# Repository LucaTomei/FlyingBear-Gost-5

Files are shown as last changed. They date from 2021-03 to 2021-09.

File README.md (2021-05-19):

# FlyingBear-Gost-5

This repository contains structural and firmware side changes applicable on the Flyingbear Ghost 5 3D printer.
The changes on the software side can be applied on the STOCK version printer or with TMC2209 driver changes.

## [Ricambi e upgrades](https://www.1612.it/wp/ricambi-e-upgrades-flying-bear-ghost-5/)

## Repository Content

- **[Firmwares](Firmwares)**
- **[Projects](Projects)**
- **[Installation Videos](Installation_Videos)**
- **[Guides](Guides)**
- **[Slicers](Slicers/README.md)**
- **[Other](Other)**

## Useful Links

- [Calibrazione Step](https://www.stampa3d-forum.it/articoli/guide/regolazione-step-mm-guida-calibrazione-assi-x-y-z/)
- [**Italy Makers - Flying Bear Ghost Facebook group**](/groups/907067056500590)
- [**Flyingbear Italian Community**](https://fbghostita.miraheze.org/wiki/Pagina_principale)
- [Russian Wiki](https://flyingbear.info/ru/решения)
- **GCODE Analyzer**
    - [Online version](http://www.gcodeanalyser.com)
    - [GitHub Repo](https://github.com/syue87/GCodeAnalyser)

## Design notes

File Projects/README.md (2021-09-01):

# Projects for Flyingbear Ghost 5

## [Smart Led](Smart_Led/README.md)

## [Octoprint PSU control case](Octoprint_PSU/README.md)

## [Russian Upgrades](CHUCHATV_Upgrades)

## [Manual Bed Leveling Project](Bed_Leveling/README.md)

### Case

- [Case in this repository with gcode files](Copertura_plexiglass/README.md)
- [Case with door](https://www.thingiverse.com/thing:4190488)

### Tool Holders

- [Tool Stand 1](https://www.thingiverse.com/thing:4067472)
- [Tool Stand 2](https://www.thingiverse.com/thing:4045895)
- [Tool Stand 3](https://www.thingiverse.com/thing:3548716)
- [Tool Stand 4](https://www.thingiverse.com/thing:4265119)
- [Tool Stand 5 - For Thermalbox](https://www.thingiverse.com/thing:4794188)
- [Tool Stand 6](https://www.thingiverse.com/thing:4736121)

### CLips 
- [Clip for extruder](https://www.thingiverse.com/thing:4267787)
- [Filament Holder](https://www.thingiverse.com/thing:4749552)
- [Bowdend Clip](https://www.thingiverse.com/thing:4613639)

### Cameras
- [Raspberry Infrared Camera](Raspberry_Infrared_cam/README.md)
- [Raspberry Cam](Raspberry_Cam/README.md)
- 
- [My Esp32 camera holder]()
- [Camera Holder - Logitech C525](https://www.thingiverse.com/thing:4667948)
- [Camera Holder - Pi Camera](https://www.thingiverse.com/thing:4390399/files)
- [Esp Camera](https://www.thingiverse.com/thing:4713405)
- [IP Camera Holder](https://www.thingiverse.com/thing:4779987)

### Printer Parts

- [Printer Foot 1](https://www.thingiverse.com/thing:4683217)
- [Printer Foot 2](https://www.thingiverse.com/thing:4702313)
- [Micro SD Holder](https://www.thingiverse.com/thing:4707808)
- [Filament Guide](https://www.thingiverse.com/thing:4704848)
- [Z Axis Support](https://www.thingiverse.com/thing:4686040)
- [Adjustable Bed Screw](https://www.thingiverse.com/thing:4583235)
- [Touchpen Holder 1](https://www.thingiverse.com/thing:4691468)
- [Touchpen Holder 2](https://www.thingiverse.com/thing:4606683)
- [Screen Cover](https://www.thingiverse.com/thing:4238913)

## [Oversized Fan Mod](ventola_maggiorata/README.md)

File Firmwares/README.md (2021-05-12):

# Firmwares for Flyingbear Ghost 5

[Official Firmwares Link](https://drive.google.com/drive/u/0/folders/1ZUuk_V8Bdn0Vt0OC19J2wQ0Nd3v5MbL4)

## Original Drivers

 - [STOCK v 5.9.1](Original_Drivers/Ghost_5_firmwarev5.91.zip)
 - [STOCK v 5.8](Original_Drivers/Ghost_5_firmware_V5-8.zip)
 - [Original with 5-point calibration (v. 5.8)](Original_Drivers/Ghost_5_firmware_V5-8-Modificato.zip)
 - [Original with 5-point calibration (v. 5.9.1)](Original_Drivers/Ghost_5_firmware_V5-91-Modificato.zip)
 - [Simone Carnio Firmware](Original_Drivers/STOCK_Firmware_Simone_Carnio_GH5.zip)

## For TMC2209

- [Original with 5-point calibration (v. 5.9.1) with all TMC2209](TMC22XX/Ghost_5_firmware_V5-91[TMC2209]-Modificato.zip)
- [Red Edition](TMC22XX/Flying-Bear-Ghost-5-Marlin-2.0-Firmware-Red3D-Edition-1.0.3.zip)

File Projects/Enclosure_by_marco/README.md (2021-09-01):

# FlyingBear Ghost 5 enclosure: top cover and front cover/door

Finally I decided to buy another 3D printer, this time I choose the FlyingBear Gost 5. I buy it because for 250 € it has solved many problems of other printers like Ender or Artillery (with the same price).

I made a case because I would like to print a more dangerous material like ABS, and to do that I create two different rears of the top cover, one standard and one with a fan for extracting harmful fumes.

<ol><li><a rel="noreferrer noopener" href="https://www.mischianti.org/2021/07/05/flyingbear-ghost-5-enclosure-top-cover/" target="_blank">FlyingBear Ghost 5 enclosure: top cover</a></li><li><a href="https://www.mischianti.org/2021/07/09/flyingbear-ghost-5-enclosure-front-cover-door/" target="_blank" rel="noreferrer noopener">FlyingBear Ghost 5 enclosure: front cover/door</a></li></ol>

FlyingBear Ghost 5 enclosure photo

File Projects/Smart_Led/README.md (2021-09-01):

# Ikea Dioder - Versione Smart

Questo progetto è nato per poter alimentare direttamente, tramite il pin vuoto della stampante, delle semplici strisce LED (non smart) rendendole smart attraverso un relè.

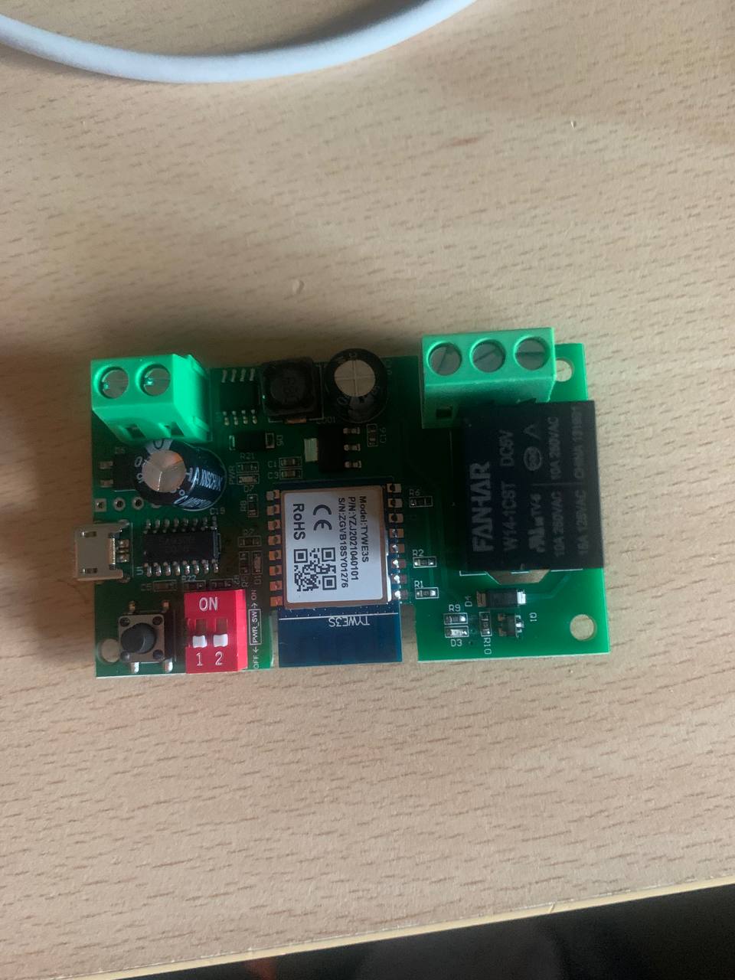
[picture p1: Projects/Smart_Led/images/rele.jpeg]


Consiglio: Dato che il relè in questione può anche essere alimentato via usb vi consiglio di configurarlo con la sua app nativa (SmartLife) prima di effettuare il cablaggio tramite stampante in modo tale che una volta effettuato il collegamento dei cavi elettrici il tutto sia già configurato e pronto all'uso.

## Occorrente

- [Ikea Dioder](https://www.ikea.com/us/en/p/dioder-led-4-piece-light-strip-set-white-20119418/) o qualsiasi altra striscia led 
- [Relé SmartLife](https://www.amazon.it/gp/product/B07SNBKXH5/ref=ppx_yo_dt_b_asin_title_o00_s00?ie=UTF8&psc=1) o qualsiasi altro relè smart
- Cavi connettore JST XH2.54 2 pin:
    - [Link Aliexpress](https://it.aliexpress.com/item/32954418743.html?spm=a2g0s.9042311.0.0.27424c4djxtsz4)
    - [Link Amazon](https://www.amazon.it/Connettore-Connettori-Espansione-Intestazione-XH2-54-2P/dp/B08P3JN1MQ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ÅMÅŽÕÑ&dchild=1&keywords=JST+XH2.54&qid=1630515821&sr=8-1)
- Comune nastro isolante

## Schema Cablaggio

Per cablare il tutto puoi scegliere se alimentare il relè e i led ad esso collegati connettendo il relè direttamente ad un pin della scheda madre oppure se alimentarlo tramite alimentatore della stampante. Di seguito verranno mostrate le due modalità di montaggio:

### Collegamento tramite alimentatore

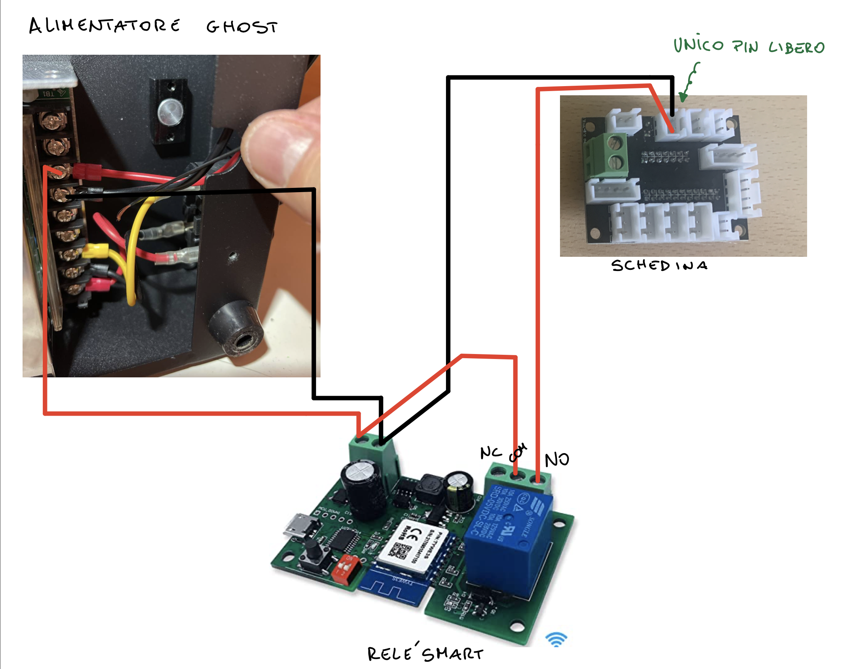
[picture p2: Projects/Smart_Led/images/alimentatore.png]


### Collegamento tramite pin della scheda madre

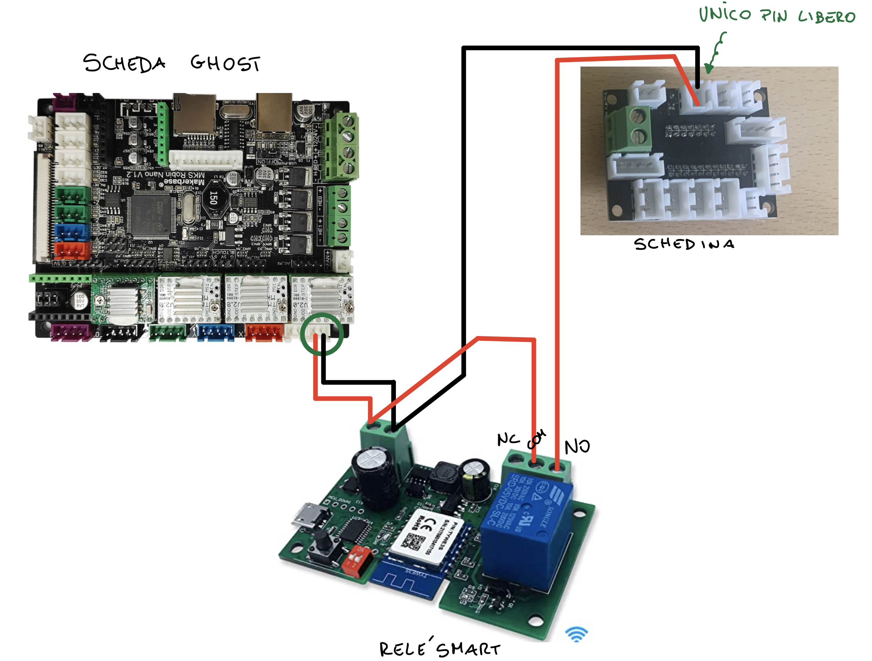
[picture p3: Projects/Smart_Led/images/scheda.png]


## Risultato Finale

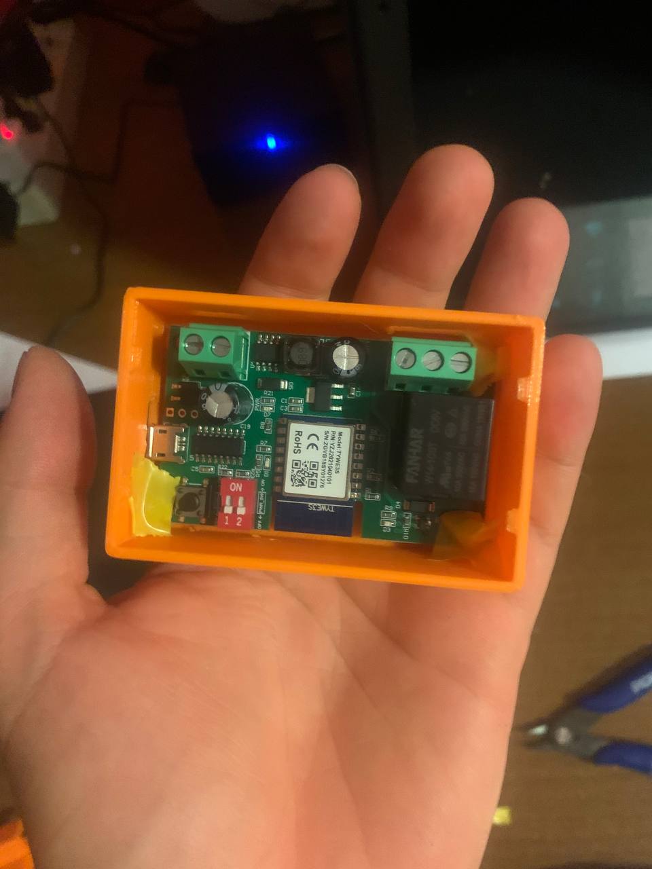
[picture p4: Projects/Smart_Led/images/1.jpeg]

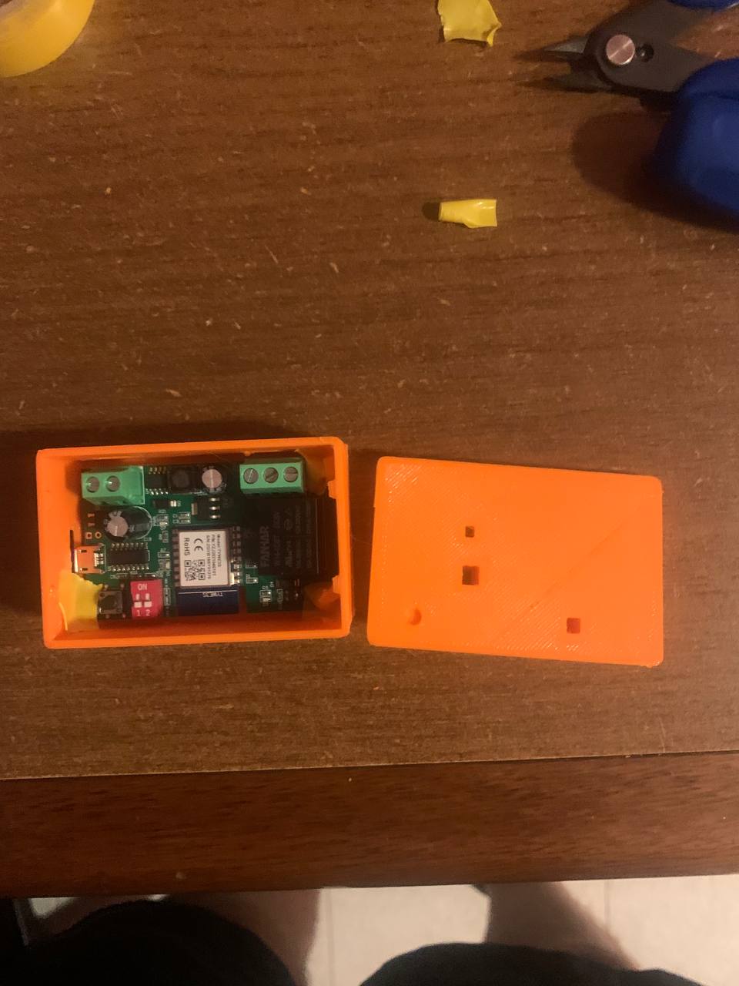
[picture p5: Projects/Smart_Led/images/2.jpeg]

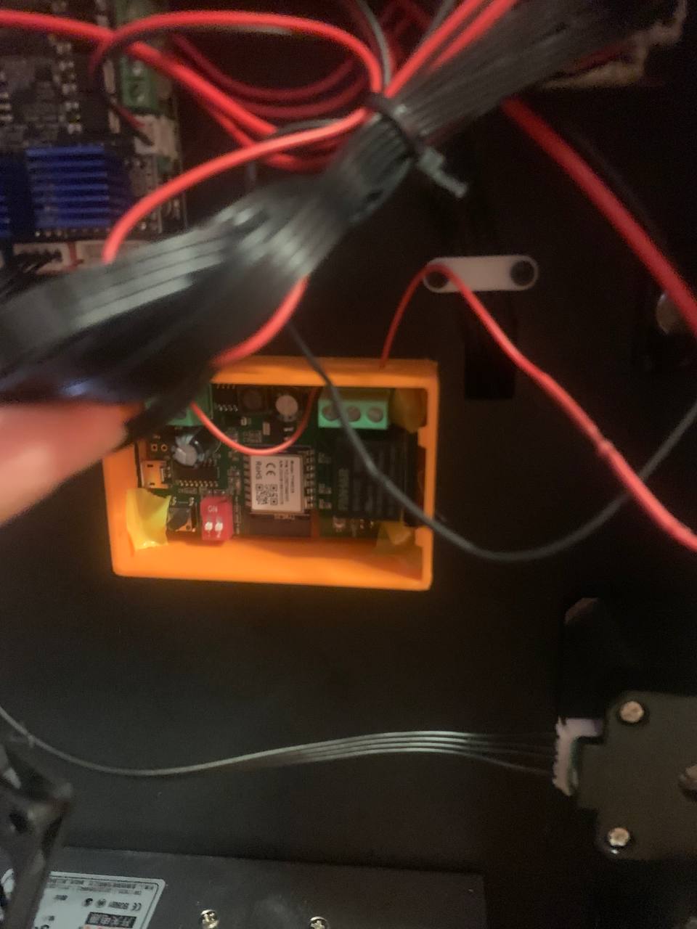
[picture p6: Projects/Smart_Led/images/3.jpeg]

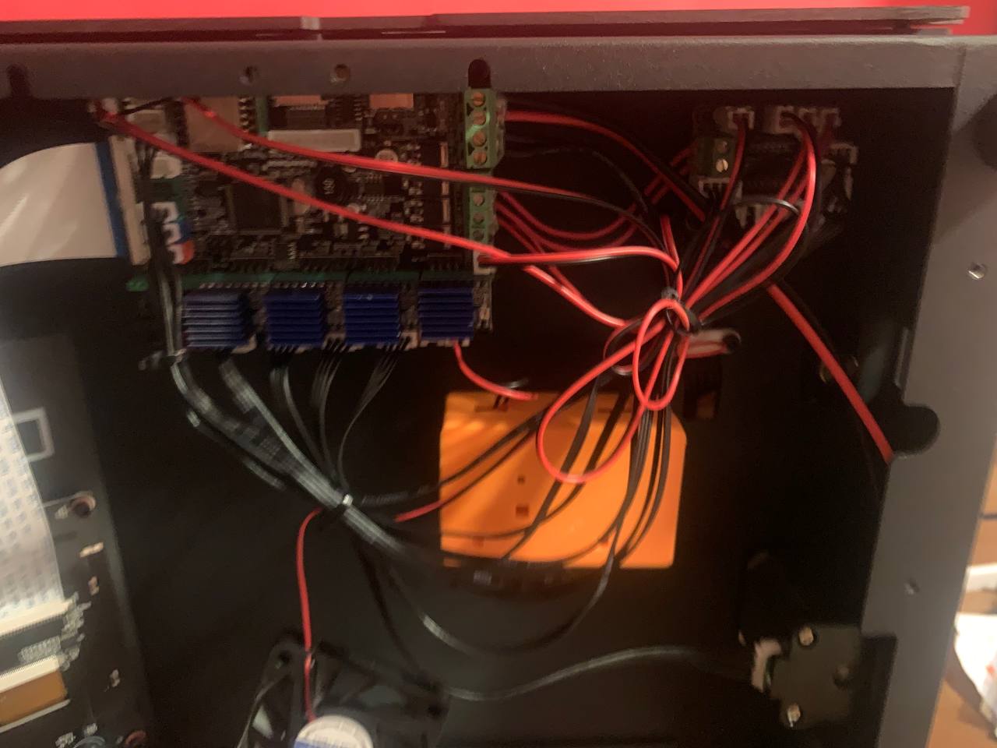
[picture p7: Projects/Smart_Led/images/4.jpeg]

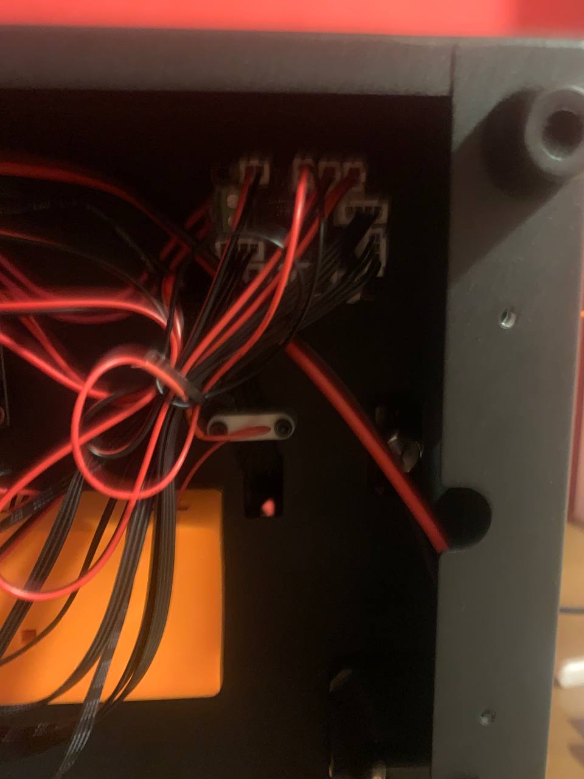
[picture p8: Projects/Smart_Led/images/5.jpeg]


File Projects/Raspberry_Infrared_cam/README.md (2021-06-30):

# Raspberry Infrared Camera Mount For Flyingbear Ghost 5

## Risultato Finale (Montaggio Alto)

<p align="center">
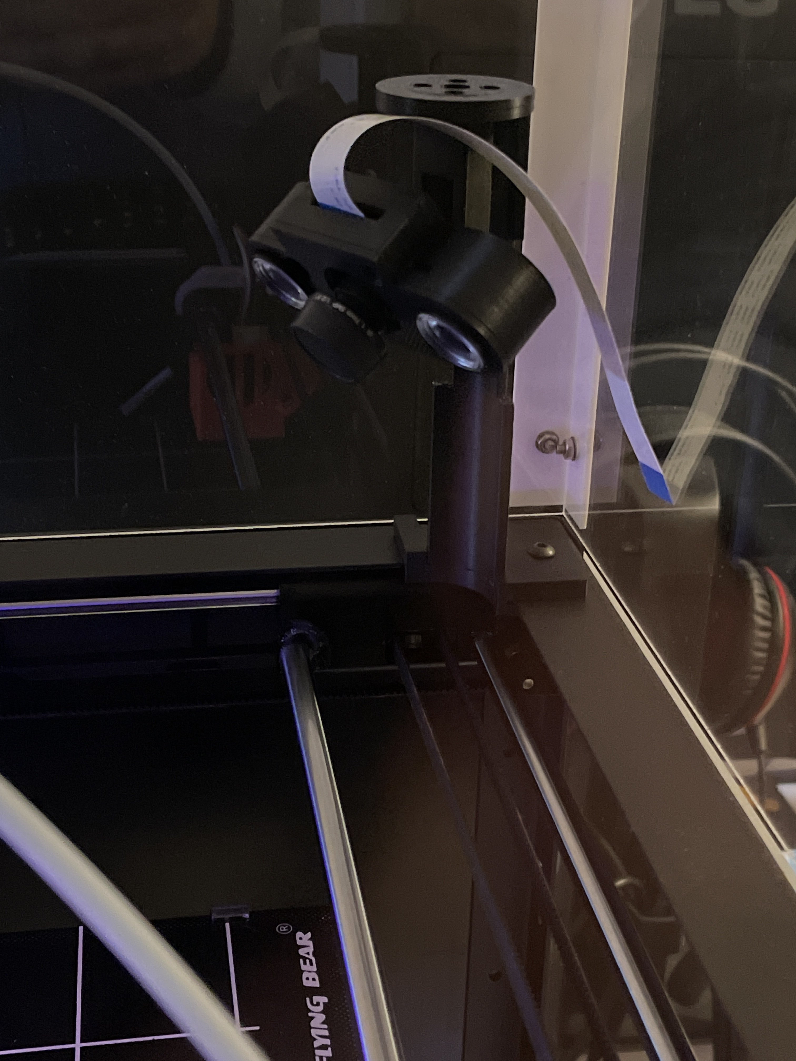
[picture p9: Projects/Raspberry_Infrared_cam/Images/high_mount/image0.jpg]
  
</p>

<p align="center">
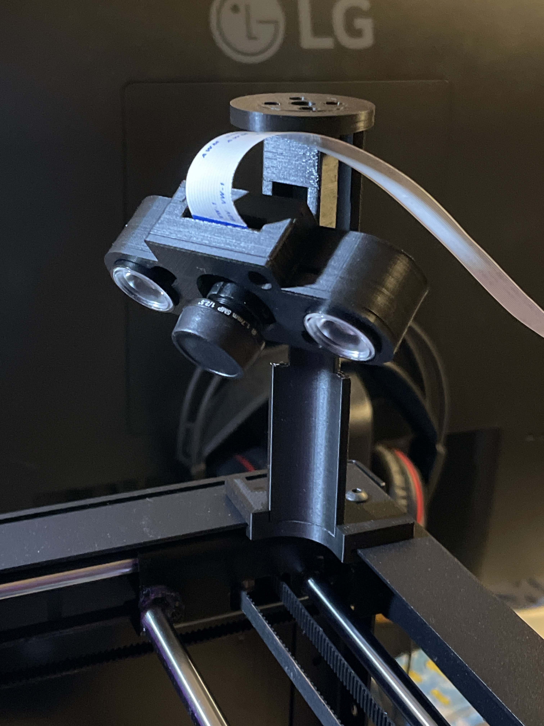
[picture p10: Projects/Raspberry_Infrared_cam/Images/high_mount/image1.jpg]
  
</p>

<p align="center">
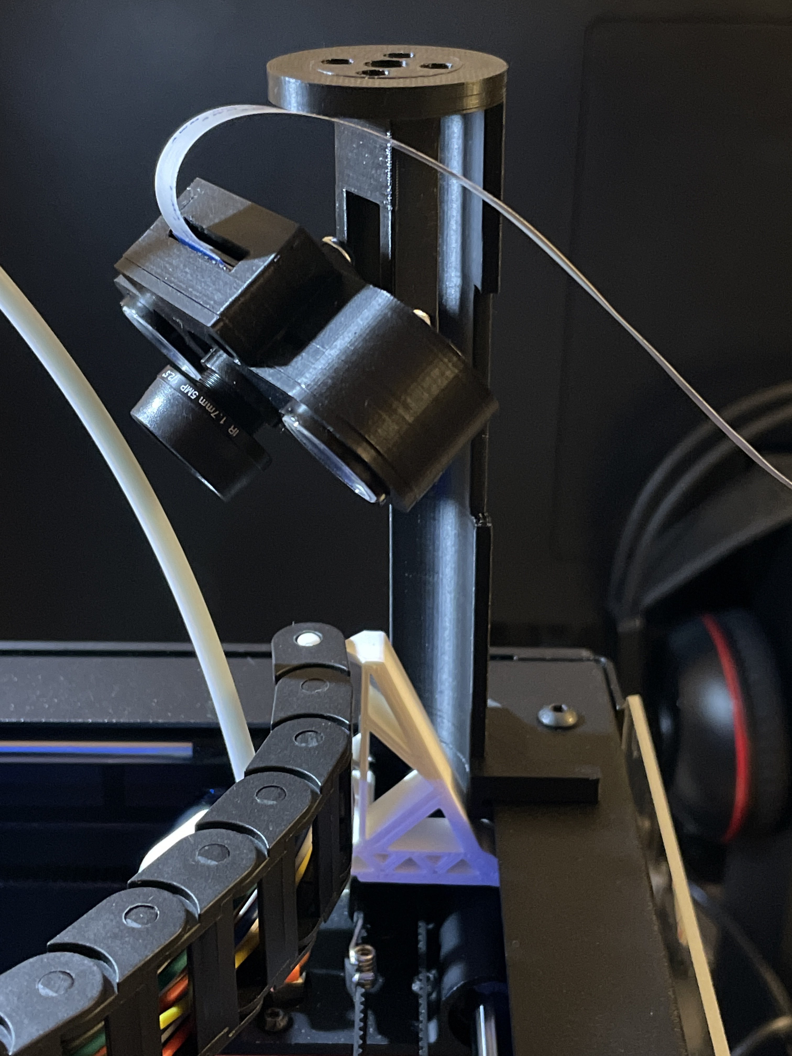
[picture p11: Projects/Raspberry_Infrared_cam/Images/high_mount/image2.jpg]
  
</p>

## Stl Files (Montaggio Alto)

- [Staffa Snodo.stl](stls/high_mount/Staffa_Snodo.stl)
- [Braccio Snodo.stl](stls/high_mount/braccio_snodo.stl)
- [Base Cover.stl](stls/high_mount/base_cover.stl)
- [Coperchio](stls/high_mount/coperchio.stl)
- [Base Supporto Angolo](stls/high_mount/base_supporto_angolo.stl)
- [Staffa Supporto Angolo](stls/high_mount/staffa_supporto_angolo.stl)

## Risultato Finale (Montaggio Piatto)

<p align="center">
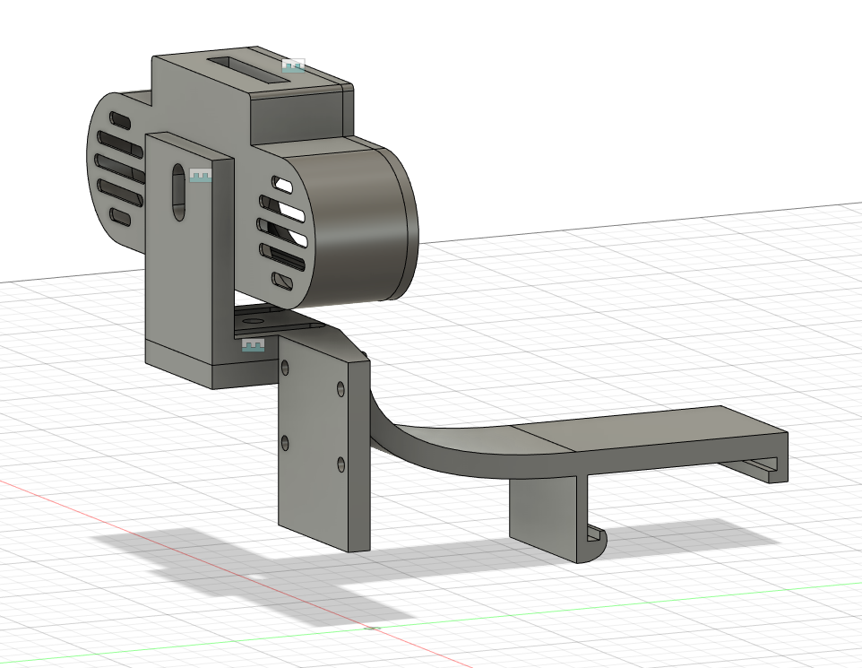
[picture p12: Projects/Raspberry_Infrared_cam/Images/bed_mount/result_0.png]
  
</p>

<p align="center">
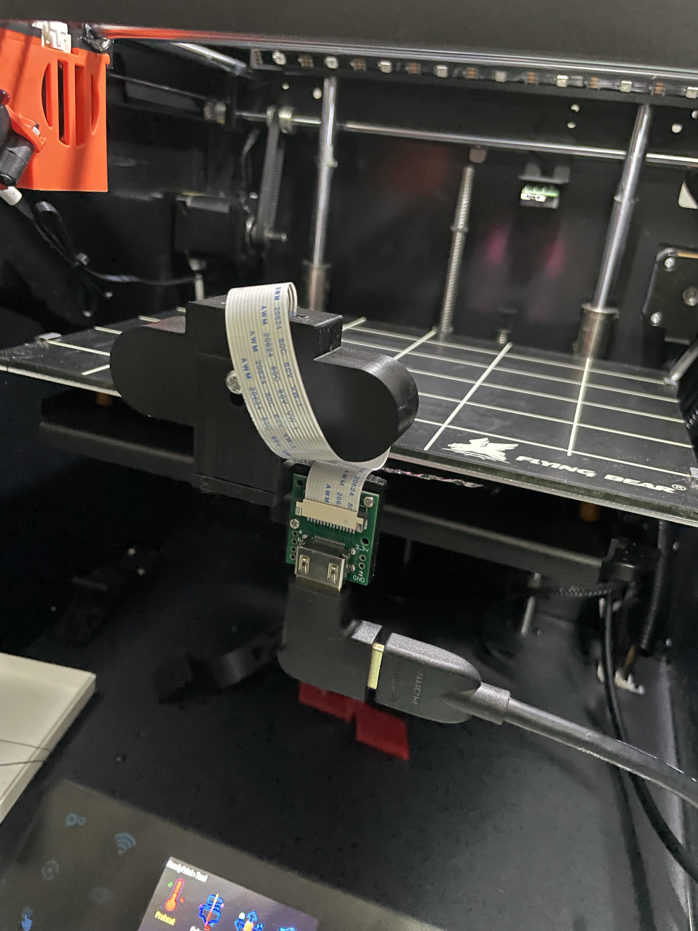
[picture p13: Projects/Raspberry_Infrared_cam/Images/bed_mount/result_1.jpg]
  </p>

<p align="center">
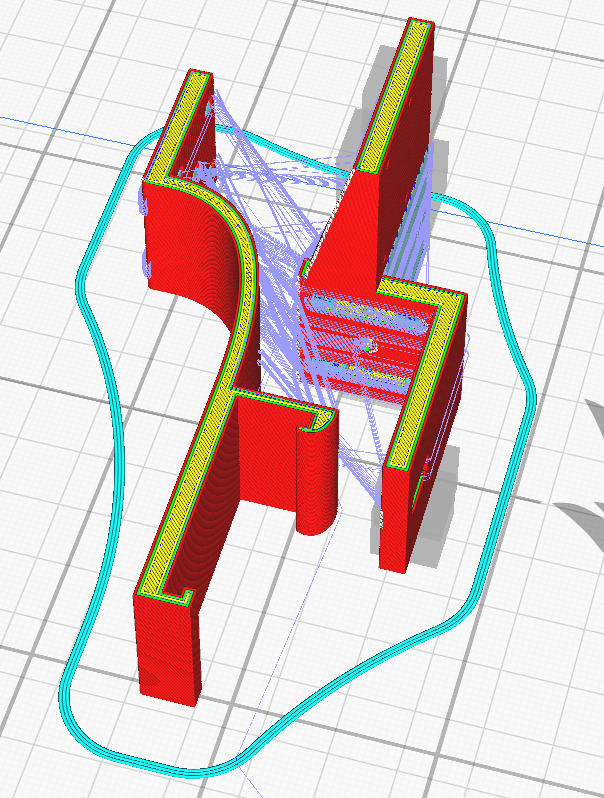
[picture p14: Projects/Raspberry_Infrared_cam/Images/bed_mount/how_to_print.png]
  </p>

<p align="center">
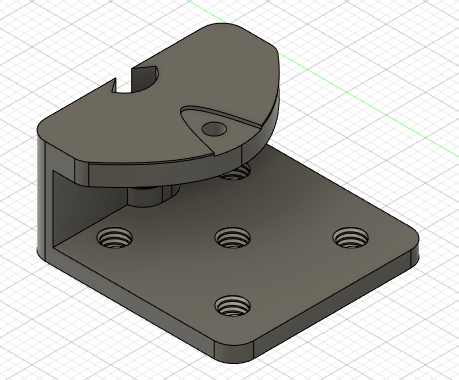
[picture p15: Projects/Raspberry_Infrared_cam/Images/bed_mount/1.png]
  </p>
  
  <p align="center">
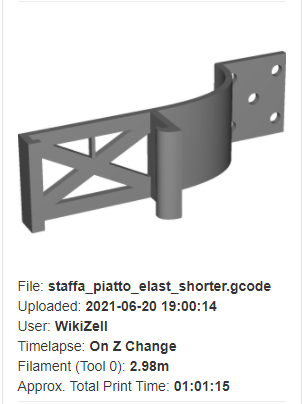
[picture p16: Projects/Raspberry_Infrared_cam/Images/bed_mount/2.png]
  </p>

<p align="center">
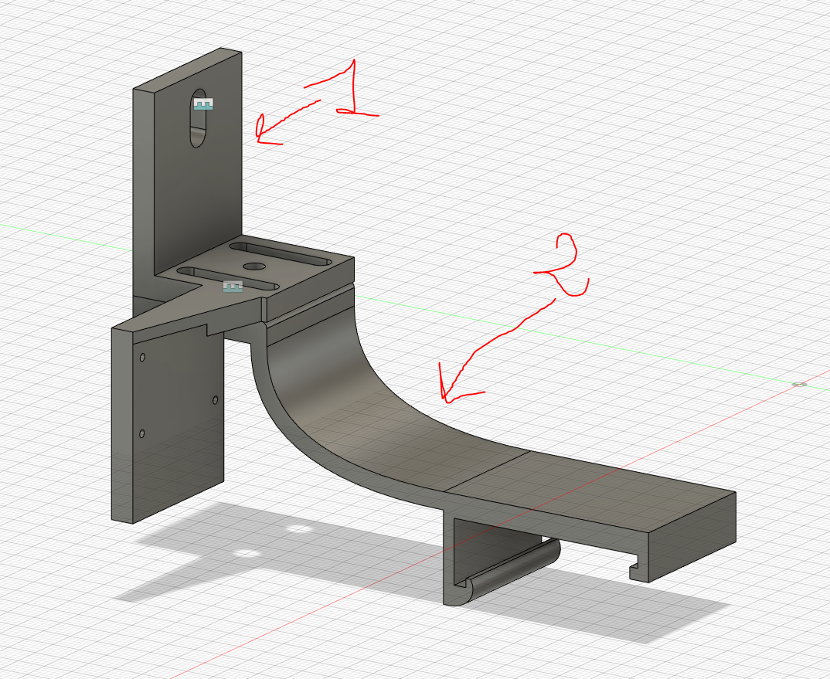
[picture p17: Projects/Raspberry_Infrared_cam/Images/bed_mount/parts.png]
  </p>

## Stl Files (Montaggio Piatto)

- [Supporto Piatto](stls/bed_mount/bed_braket.stl)
- [Adattatore Supporto](stls/bed_mount/adapter_bracket.stl)
- [Adattatore Supporto NO HDMI](stls/bed_mount/adapter_bracket_NO_HDMI.stl)

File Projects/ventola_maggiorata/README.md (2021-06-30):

# Ventola Maggiorata 

Se anche voi avete bisogno di un maggiore flusso d'aria per la ghost o solamente per sostituire la ventola stock rumorosa con una più grande vi basterà seguire questa semplice guida.

## Risultato Finale

 <p align="center">
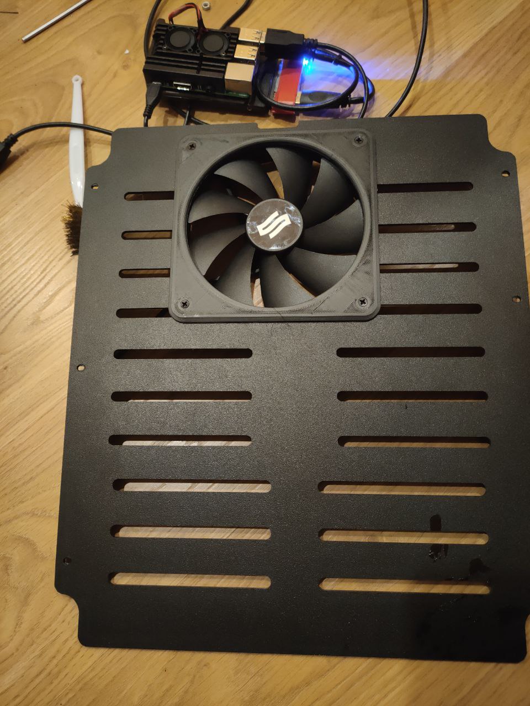
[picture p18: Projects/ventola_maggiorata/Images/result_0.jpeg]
  </p>
<p align="center">
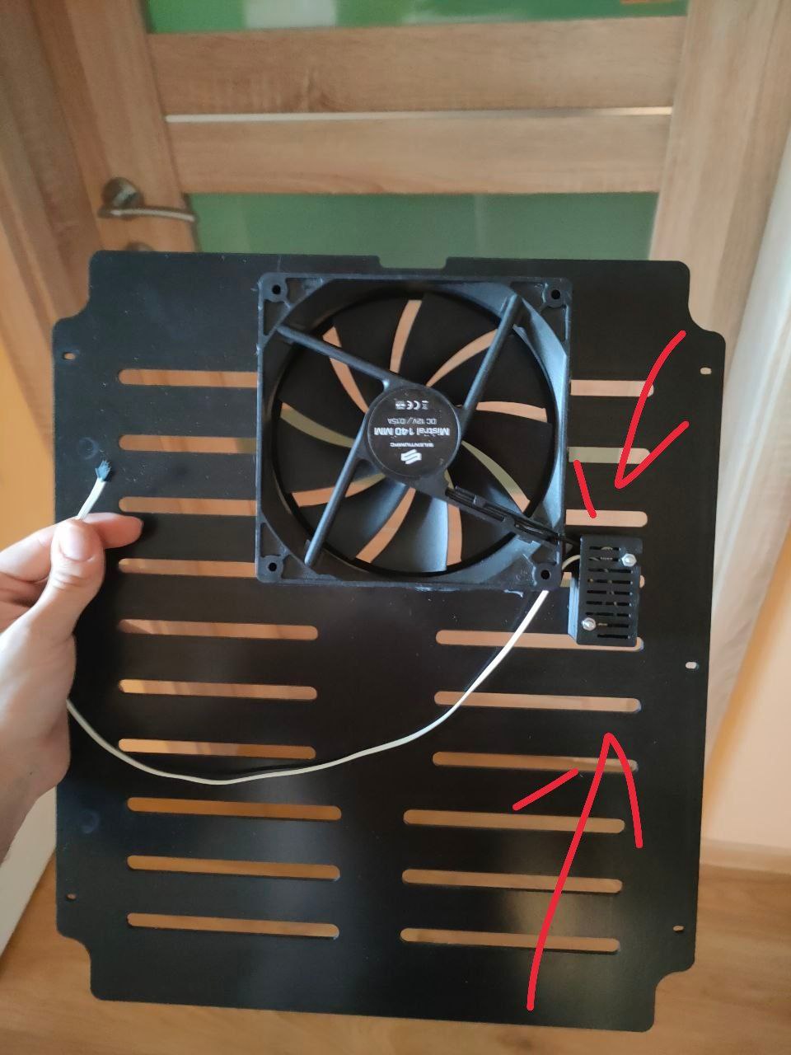
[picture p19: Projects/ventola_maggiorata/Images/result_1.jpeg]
  </p>
  <p align="center"> **Rialzo per Piedini**
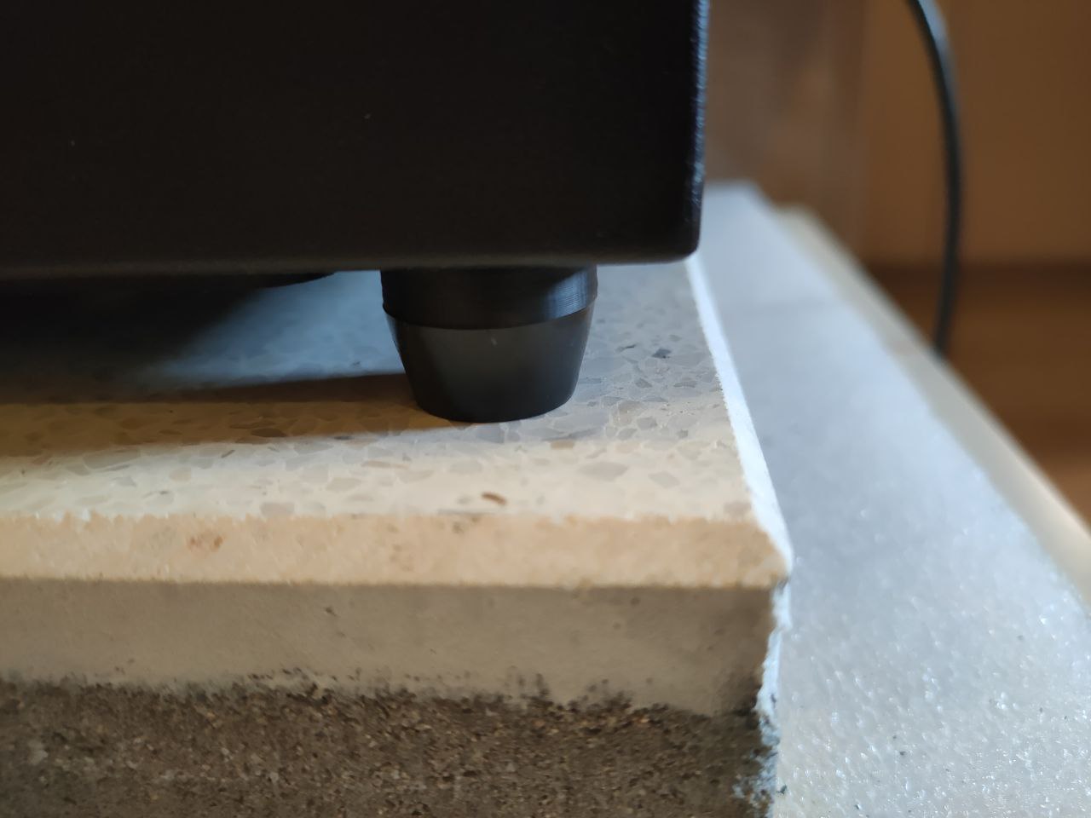
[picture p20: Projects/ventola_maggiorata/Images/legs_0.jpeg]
  </p>
  <p align="center">
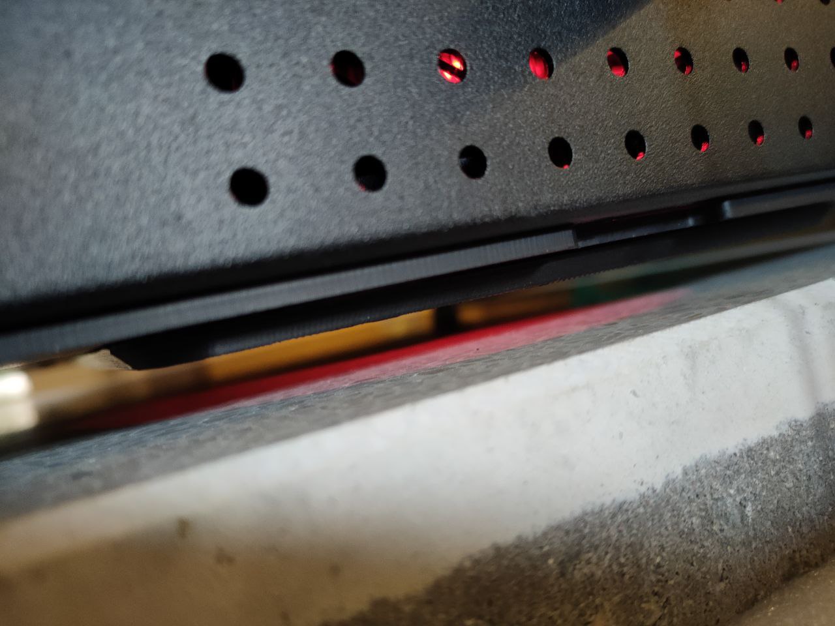
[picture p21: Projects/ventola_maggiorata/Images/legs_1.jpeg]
  </p>

## Files Stl

- [Case ventola](stls/danduck.stl)
- [Rialzo Piedini](stls/legs.stl)
- [Case Buck Converter bottomo](stls/module_case_bottom.stl)
- [Case Buck Converter Top](stls/module_case_top.stl)

## Occorrente

- [Buck Converter](https://a.aliexpress.com/_uXTZmX): Serve a convertire i 24v della ghost in 12v o 5v
- Qualsiasi ventola da 140mm, per esempio una [Noctua](https://www.amazon.it/Noctua-NF-A14-ULN-Ventola-140/dp/B00AA89BN4/ref=sr_1_2_sspa?__mk_it_IT=ÅMÅŽÕÑ&dchild=1&keywords=140mm+ventola+silenziosa&qid=1620474844&sr=8-2-spons&psc=1&smid=A38F5RZ72I2JQ&spLa=ZW5jcnlwdGVkUXVhbGlmaWVyPUEzVjJaRFhQQUFTM1JYJmVuY3J5cHRlZElkPUEwMDM5MDMyMTIySzI5SDRFU0kwSiZlbmNyeXB0ZWRBZElkPUEwODQ3MTM1T0tTV0xWODJYQ0tUJndpZGdldE5hbWU9c3BfYXRmJmFjdGlvbj1jbGlja1JlZGlyZWN0JmRvTm90TG9nQ2xpY2s9dHJ1ZQ==)

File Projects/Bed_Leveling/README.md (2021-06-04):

# Manual Bed Leveling

Tale progetto premette un migliore livellamento manuale della nostra Ghost 5 attraverso l'utilizzo di un comparatore centesimale ad orologio.

## Risulatot Finale

<p align="center">
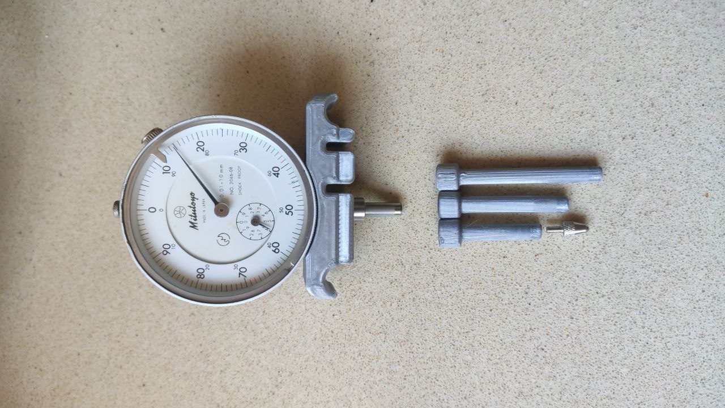
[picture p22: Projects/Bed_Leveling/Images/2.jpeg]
  
</p>

<p align="center">
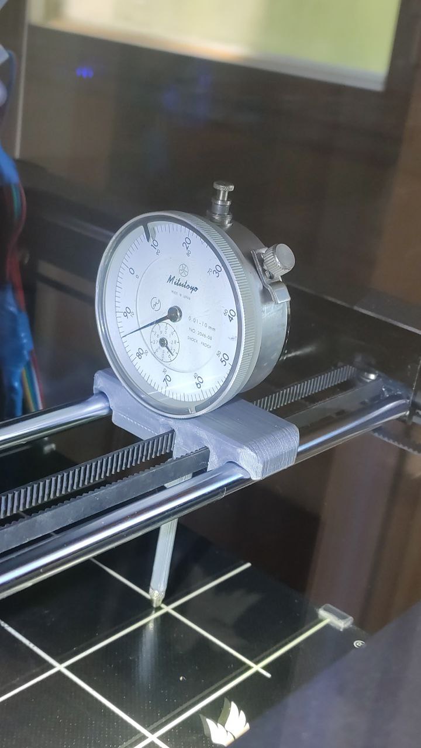
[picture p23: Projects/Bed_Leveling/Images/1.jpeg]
  
</p>

## Link d'acquisto
- [Amazon Spedizione Lenta](https://www.amazon.it/dp/B08GCGK2CP/)
- [Amazon Spedizione Veloce](https://www.amazon.it/dp/B07CRHKDZ9)
- [Aliexpress](https://it.aliexpress.com/item/32955622774.html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)

## Stls
- [Base per Indicatore](Base_for_indicator.STL)
- [Estender 50](Extender_50.STL)
- [Extender 45](Extender_45.STL)
- [Extender 40](Extender_40.STL)

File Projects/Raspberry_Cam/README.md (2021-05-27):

# RaspberryCamera Mount For Flyingbear Ghost 5

## Risultato Finale

<p align="center">
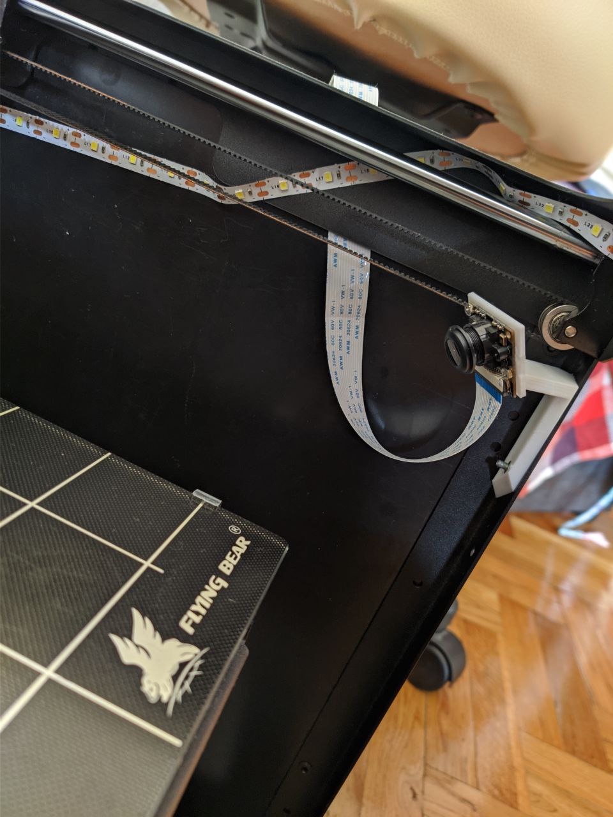
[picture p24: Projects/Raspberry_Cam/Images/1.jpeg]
  
</p>

## Stl Files

- [Support Angolo](stls/cam_angle_high.stl)
- [Camera Mount](stls/pi_cam_thin.stl)

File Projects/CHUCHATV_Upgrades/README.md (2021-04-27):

# [Best russian upgrades](https://plati.market/itm/2973079?lang=en-US)

## Content

1. Folder 1 mechanical fastening:

    - Folder 3D printing (3D PRINT STL IPT) - files in STL format for Printing + IPT format Autodesk Inventor Professional 2017 for editing 
    - Folder Engraving - DWG files for logo engraving 
    - Firmware V5-8 folder - the latest factory firmware, but with the changes made for 4988 drivers. 
    - Folder Cutting acrylic - files for laser cutting acrylic in DWG format + IPT format Autodesk Inventor Professional 2017 + photo 
    - Fitting drawings with REAL dimensions of the Flyingbear Ghost 5 printer, for possible installation of acrylic panels on the Flyingbear Ghost 4c 

    But, if you need a full-fledged 3D model of the FlyingBear Ghost 5 Factory Printer in IPT Autodesk or STEP format, you can buy it separately in my store https://plati.market/itm/3036725?lang=en-EN 

1. NEW E3DV6 STL and IPT folder - there is a new hot end head, files in STL format for Printing + IPT format Autodesk Inventor Professional 2017 for editing 

2. The Additional box for drying plastic folder is a new addition to the heat chamber, which allows you to dry plastic directly in the box during printing. 

    - Folder 3D PRINT STL and IPT-files in STL format for Printing 
    - Folder Cutting acrylic - files for laser cutting acrylic in DWG format 

4. Estimate (Estimate) in xl format - there is a basic estimate and two additional ones for installing a direct extruder with a factory head or with my upgraded from Chucha TV

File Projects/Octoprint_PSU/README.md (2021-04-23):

# Octoprint PSU Control

Se desideri controllare lo spegnimento e l'accensione della tua stampante 3D tramite octoprint, questo progetto fa per te.

## Occorrente

- **Raspberry 3b/4**
    - [Aliexpress Link](https://a.aliexpress.com/_m0tWtj5)
    - [Amazon Link](https://www.amazon.it/RASPBERRY-PI-Raspberry-Desktop-Computer/dp/B00LPESRUK/ref=sr_1_1?__mk_it_IT=ÅMÅŽÕÑ&dchild=1&keywords=raspberry+3b+plus&qid=1619095034&sr=8-1)
- **Cavo Alimentazione Stampante**
    - [Aliexpress Link](https://a.aliexpress.com/_mKopqwr)
    - [Amazon Link](https://www.amazon.it/Lindy-30346-Cavo-Alimentazione-Angolo/dp/B0058H0XGQ/ref=sr_1_12?__mk_it_IT=ÅMÅŽÕÑ&dchild=1&keywords=iec+320+c13&qid=1619095365&sr=8-12)
- **IEC 320 Maschio**
    - [Aliexpress Link](https://a.aliexpress.com/_mKz5twx)
    - [Amazon Link](https://www.amazon.it/AERZETIX-connettori-Alimentazione-Computer-Stampante/dp/B07Z3F3WT8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ÅMÅŽÕÑ&dchild=1&keywords=iec+320+c13+presa&qid=1619095721&sr=8-26)
- **IEC 320 Femmina**
    - [Aliexpress Link](https://a.aliexpress.com/_mLllDhZ)
    - [Amazon Link](https://www.amazon.it/Sourcingmap-terminali-pannello-connettore-alimentazione/dp/B00HUHAB0U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ÅMÅŽÕÑ&dchild=1&keywords=iec+320+c14&qid=1619095340&sr=8-4)
- **5V Raspberry Relay 1 Canale**
    - [Aliexpress Link](https://it.aliexpress.com/item/33036673478.html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,searchweb201602_,searchweb201603_)
    - [Amazon Link](https://www.amazon.it/ARCELI-KY-019-Channel-Module-arduino/dp/B07BVXT1ZK/ref=sr_1_8?__mk_it_IT=ÅMÅŽÕÑ&dchild=1&keywords=raspberry+5v+relay&qid=1619095807&sr=8-8)
- **Cavi a ponticello per Arduino/Raspberry**
    - [Aliexpress Link](https://it.aliexpress.com/item/1005002000655439.html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,searchweb201602_,searchweb201603_)
    - [Amazon Link](https://www.amazon.it/AZDelivery-Cavetti-Maschio-Femmina-Raspberry/dp/B074P726ZR/ref=sr_1_3_sspa?__mk_it_IT=ÅMÅŽÕÑ&dchild=1&keywords=cavi+arduino&qid=1619095849&sr=8-3-spons&psc=1&smid=A1X7QLRQH87QA3&spLa=ZW5jcnlwdGVkUXVhbGlmaWVyPUExOTNVSlBIUDBOM0c2JmVuY3J5cHRlZElkPUEwMDg2ODU5M1FURTdCQTM3S043RCZlbmNyeXB0ZWRBZElkPUEwMjkxNjQ4MzQ0TFpMOFhLRFNZMyZ3aWRnZXROYW1lPXNwX2F0ZiZhY3Rpb249Y2xpY2tSZWRpcmVjdCZkb05vdExvZ0NsaWNrPXRydWU=)
- **IEC 320 Prolunga**
    - [Aliexpress Link](https://a.aliexpress.com/_mMmK1I7) 
    - [Amazon Link](https://www.amazon.it/dp/B004787EU0/ref=cm_sw_r_cp_api_glt_i_64ATZ65C4ZHDVQ1WMWEJ)
- **Ventola Raspberry 3cm** (Opzionale)
    - [Aliexpress Link](https://it.aliexpress.com/item/32961250837.html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,searchweb201602_,searchweb201603_)
    - [Amazon Link](https://www.amazon.it/MakerHawk-Raspberry-Brushless-Connector-Separating/dp/B071JN6HKM/ref=sr_1_2?__mk_it_IT=ÅMÅŽÕÑ&dchild=1&keywords=raspberry+3mm+ventola&qid=1619096033&sr=8-2)

## Struttura (STL)

- [Scatola](Octoprint_box_bottom.stl)
- [Copertura Scatola](stls/Octoprint_box_upper.stl)

## Guida Completa

<p align="center">
  
</p>

<p align="center">
  
</p>

<p align="center">
  
</p>

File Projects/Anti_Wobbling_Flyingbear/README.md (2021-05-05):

# Anti Wobbling per Flyingbear Ghost 5

In questa cartella sono presenti due progetti, sta a voi la scelta:
- [Progetto 1](1/README.md)
- [Progetto 2](2/README.md)

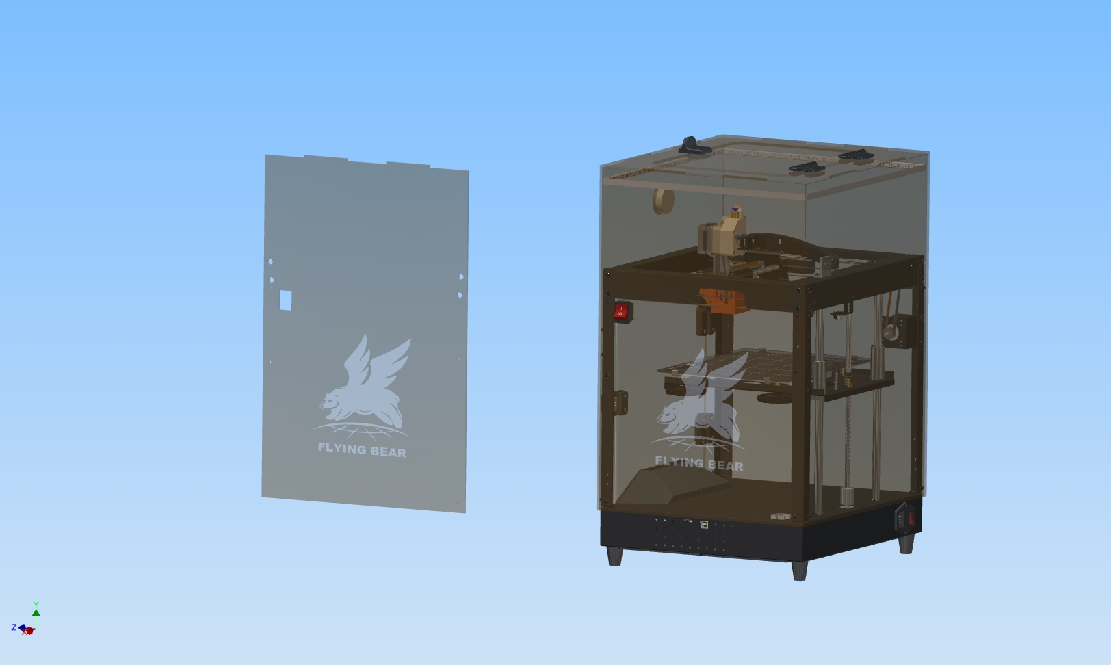
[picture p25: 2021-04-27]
Projects/CHUCHATV_Upgrades/1 mechanical fastening/Engraving/Right lateral BEAR ENGRAVING.jpg

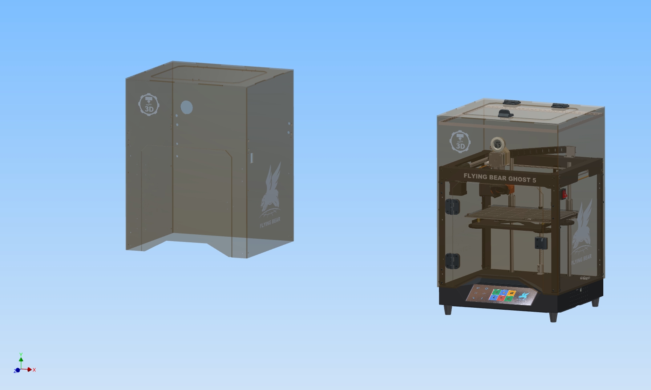
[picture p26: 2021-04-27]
Projects/CHUCHATV_Upgrades/1 mechanical fastening/cutting acrylic/mechanical fastening of the cover4.jpg

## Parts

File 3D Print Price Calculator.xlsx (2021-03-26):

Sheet: Instruction
 | Add this Spreadshee to your Google Drive by Clicking on File > Make a copy
 | Quick Set Up
1 | Go to Depreciation tab, and insert your 3D printer price | Click Here (https://docs.google.com/spreadsheets/d/17cFOijYvJ2LXwd66NKCaNe8qkb9bHx2R2kau7wYZ2uo/edit)
2 | How much will your 3D printer work in period of one year | Click Here (https://docs.google.com/spreadsheets/d/17cFOijYvJ2LXwd66NKCaNe8qkb9bHx2R2kau7wYZ2uo/edit)
3 | Measure how much power does your 3D printer consumer over an hour | Click Here (https://docs.google.com/spreadsheets/d/17cFOijYvJ2LXwd66NKCaNe8qkb9bHx2R2kau7wYZ2uo/edit)
4 | Insert price of power per hour (check your power bills) | Click Here (https://docs.google.com/spreadsheets/d/17cFOijYvJ2LXwd66NKCaNe8qkb9bHx2R2kau7wYZ2uo/edit)
5 | Set up Material Price and Nett Mass | Click Here (https://docs.google.com/spreadsheets/d/17cFOijYvJ2LXwd66NKCaNe8qkb9bHx2R2kau7wYZ2uo/edit)
 | How To use Calculator
1 | Import your 3D modelin in Slicer
2 | From your Slicer use Print Time Estimate to insert into calculator | Insert 3D Print Time (https://docs.google.com/spreadsheets/d/17cFOijYvJ2LXwd66NKCaNe8qkb9bHx2R2kau7wYZ2uo/edit)
3 | Also from Slicer use calculate 3D printed Part Mass | Insert Primary Material Mass (https://docs.google.com/spreadsheets/d/17cFOijYvJ2LXwd66NKCaNe8qkb9bHx2R2kau7wYZ2uo/edit)
4 | If Support Material is the same as Primary Material, leave 0 g Mass for support
5 | If you are using diferent Support Material, insert Support Material Mass | Insert Support Material Mass (https://docs.google.com/spreadsheets/d/17cFOijYvJ2LXwd66NKCaNe8qkb9bHx2R2kau7wYZ2uo/edit)
6 | Insert how much did you speed time on preparing to start 3D print | Operator Time (https://docs.google.com/spreadsheets/d/17cFOijYvJ2LXwd66NKCaNe8qkb9bHx2R2kau7wYZ2uo/edit)
7 | Insert how much time will you spend on cleaning the model after the 3D print (support removal) | Post-Process Time (https://docs.google.com/spreadsheets/d/17cFOijYvJ2LXwd66NKCaNe8qkb9bHx2R2kau7wYZ2uo/edit)
8 | Insert Percentage which represents your profit from 3D printing Service | Profit (https://docs.google.com/spreadsheets/d/17cFOijYvJ2LXwd66NKCaNe8qkb9bHx2R2kau7wYZ2uo/edit)

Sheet: Calculator
No. | Expenses | Price | Unit | Quantity | Total
 |  |  |  |  |  | Legend
 | Machine overhead expenses |  |  |  |  | Green Fields are Input Fields
1 | 3D Printer Hour Rate | €0.84 | hour | 1 | €0.84 | Orange Fields are for tweaking price of your hourly rates
 | Material expenses
2 | Primary Material | €0.03 | g | 50 | €1.50
3 | Support Material | €0.00 | g | 0 | €0.00
4 | Scrap Rate |  |  | 0% | €0.00
 | Operator Expenses
5 | Inspecting & Repairing 3D models | €10.00 | hour | 0.5 | €5.00
6 | Preparation for 3D printing* |  |  | 0.3 | €3.00
 | Post Process Expenses
7 | Support removal Labor | €15.00 | hour | 0 | €0.00
8 | Sanding, Gluing Labor |  |  | 0 | €0.00
9 | Total cost |  |  |  | €10.34
10 | Profit |  |  | 10% | €1.03
 | 3D Printing Price |  |  |  | €11.38
 | *Preparation for 3D printing includes importing models in slicer, orienting models, adding support, setting up 3D printing parameters, change and prepare materials on Machine, starting the print etc.

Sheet: Material
Material Costs | Price | Nett Mass | Units
Primary Material | €30.00 | 1000 | g | PLA euro/kg
Support Material* | €0.00 | 1000 | g | UM PVA euro/kg
*If Primary and Support Material are the same, insert the same price and Nett Mass in Support Material Colum as well

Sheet: Depreciation
Description | Value | Units
3D Printer Cost | €350.00
3D Printer Expected Life | 3 | years
Total Working hours in a year | 500 | hours
Scrap Value | €0.00
3D Printer Hour Rate | €0.23

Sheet: Maintenance
Spare Parts | Price
Print Table Glass | €35.90
PTFE Coupler | €18.90
Belts Pack | €24.90
Nozzle | €18.90
Hot End Isolator | €34.50
Feeder pack | €36.88
Heater Cartridge | €43.90
Total per Year | €213.88
Maintenance per Hour | €0.43

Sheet: Power Consumption
Power Consmption Cost | Value | Units
Power Consumption per Hour | 1 | kWh
Power price | €0.18 | /kWh
Power Cost per Hour | €0.18

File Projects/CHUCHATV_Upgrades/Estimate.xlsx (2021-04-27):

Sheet: Estimate
 | Name | Description | quantity | price, USD | delivery | Total, USD | ссылка на товар
 | Cable channel 7 * 7mm | 1 meter | 1 | 5.9 | 0 | 5.9 | http://ali.pub/53z26k
 | Fitting | PC4-01 | 1 | 0.5 | 0.67 | 1.17 | http://ali.pub/53z2jl
 | Switch | KCD-2 | 1 | 0.5 | 0 | 0.5 | http://ali.pub/53z2p1
 | Round hygrometer | the black | 1 | 2.03 | 0.49 | 2.52 | http://ali.pub/53z2tb
 | Magnet 20 * 10 * 3 |  | 2 | 1.7 | 1 | 4.4 | http://ali.pub/53z33t
 | Fan 6010 24V | 60х60х10 | 2 | 1.71 | 0 | 3.42 | http://ali.pub/53z39g
 | Fan 4010 24V | 40х40х10 | 1 | 1 | 0 | 1 | http://ali.pub/5b3tq4
 | BIGTREETECH TMC2209 V1.2 |  | 1 | 10.38 | 0 | 10.38 | http://ali.pub/53z3ot
 | Insulation for the table | 310*310 | 1 | 2.51 | 1.31 | 3.82 | http://ali.pub/53z40h
 | Wire braid |  | 1 | 3 | 0 | 3 | http://ali.pub/53z49f
 | Raldiator sticky |  | 2 | 0.58 | 0.86 | 2.02 | http://ali.pub/53z4xx
 | LED strip SMD 5050 | IP65 Waterproof + 24V | 1 | 7.6 | 0 | 7.6 | http://ali.pub/53z57g
 | Bear Nozzles | 0.4 mm | 2 | 2 | 0 | 4 | http://ali.pub/55aa2i
 | Screws m3 * 12 | 50 pcs |  |  |  | 0
 | Screws m3 * 16 | 10 pieces |  |  |  | 0
 | Screws m3 * 16 | 10 pieces |  |  |  | 0
 | Heat chamber bearings | 8x22x7 mm 608ZZ | 10 | 1 | 3 | 4 | http://ali.pub/5b3ykc | optional, optional
Estimate for a regular Factory head
 | Titanium SHORT motor |  | 1 | 13 | 0 | 13 | http://ali.pub/53z3vf
 | Fan snail 5015 24V |  | 1 | 2 | 0 | 2 | http://ali.pub/552skb
 | Bimetal thermal barrier | D Crazy Heat Break | 1 | 9 | 0 | 9 | http://ali.pub/5a1ool | optional, optional
Estimate for ChuchaTV heads
 | E3d V6 BMG Hotend SET | set №3 for 24v Right | 1 | 44 | 0 | 44 | http://ali.pub/57c7c7
 | Turbine SNAIL 4020 | 24V | 1 | 1.2 | 0 | 1.2 | http://ali.pub/57624q
 | Bimetal NF V6 THERMOBARRIER |  | 1 | 8 | 0 | 8 | http://ali.pub/59x0mg

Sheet: TMC2208-2209
Vref - Driver voltage | Vref |  | enter values
Irms - Constant current on motors. | Irms |  | enter values
Imax - Peak current on motors | Imax |  | enter values
Vref = (Irms * 2.5) / 1.77 | Vref | 0
Irms = (Vref * 1.77) / 2.5 | Irms | 0
Imax = Irms * 1.41 | Imax | 0
Irms = Imax / 1.41 | Irms | 0

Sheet: Speed calculation
in English
Parameters | known | necessary to find out | formula | what values to set
Initial speed (Jerk) V0, mm / s |  | 0.00 | V0=V-at | V | a | t
Final speed (printing speed) V, mm / s |  | 0.00 | V=V0+at | V0 | a | t
Acceleration (ACCELERATION) a, mm / s² |  | #DIV/0! | a=(V²-V0²)/2S | V | S | V0
Time t, s |  | #DIV/0! | t=(V-V0)/a | V | a | V0
Travel S, mm |  | #DIV/0! | S=(V²-V0²)/2a | V | a | V0
Jerk enter values
ACCELERATION enter values
d- JUNCTION_DEVIATION RESULT | #DIV/0!

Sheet: Calibration instruction feeder
M302 P1; Disabling the temperature protection of the extruder
G92 E0; Resetting the extruder position
G1 E280 F800; Extrude 280mm plastic
To start setting up the steps, we need to free the filament from the printer. To do this, it is necessary to heat the nozzle to the operating temperature (the easiest way to do this is by starting the preheating of the extruder on the printer), then squeeze the filament a little (3-5 mm) towards the table, and then roll it back 7-8 cm. After this operation, you can safely pull out the filament with your hands without fear of damaging anything.
1. Take the ptfe tube out of the feeder fitting. To do this, press on the black ring on the fitting evenly and as far as possible until it stops, in this position the fitting releases the tube and it is pulled out without applying force.
2. Slightly rewind the plastic back onto the reel, an even (not melted) filament should come out of the feeder. Cut it off exactly along the edge of the fitting.
3. We go to the kuru, connect to the printer via WiFi, go to the monitor tab and send the following lines in turn to the Send g-code window
M302 P1; Disabling the temperature protection of the extruder
G92 E0; Resetting the extruder position
G1 E280 F800; Extrude 280mm plastic
It is better to choose the length of the extruded plastic based on the size of the ruler you have, extrude 10% less.
4. Cut off the extended plastic in the same way along the edge of the fitting. We measure the length of the cut piece - for example 265 mm.
5. Calculate the correct number of motor steps per mm. To do this, we take the current value of the steps (IN THE FIRMWARE by default 400), multiply by the length that was requested to extrude (in example 280) and divide by the result obtained (in example 265):
400 * 280/265 = 422.64
6. Take the robin_nano35_cfg.txt file from the firmware, find the parameter> DEFAULT_E0_STEPS_PER_UNIT in it and replace its value with the value obtained in the previous step. Save, put the file in the root of the sd card and restart the printer.
7. It is recommended to repeat the procedure from step 3.
8. Putting back the printer.
- Find out the current number of steps per mm, (command M503)
We multiply by the received coefficient.
- Introduces into the firmware, or quickly into memory: M92 E ***
Don't forget to save the M500.

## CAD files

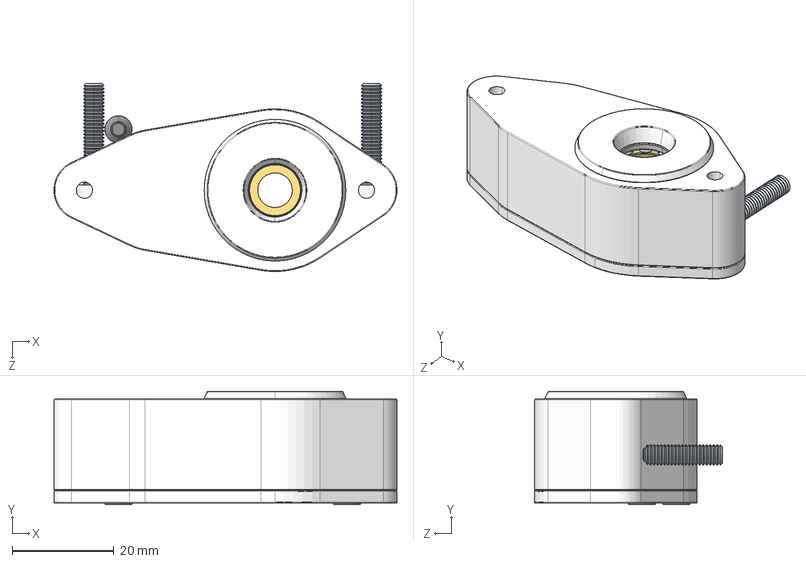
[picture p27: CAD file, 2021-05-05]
Projects/Anti_Wobbling_Flyingbear/2/stls/Assemblaggio dado.STEP
67.5 x 22.3 x 37.0 mm
Çàæèì ãàéêè 1^Óçåë ãàéêè
Ãàéêà 1^Óçåë ãàéêè
Äåòàëü4^Óçåë ãàéêè
M - 3 x 0.5 x 6 (2)_B18.3.5M - 3 x 0.5 x 10 Socket FCHS -- 10S x 6
M - 4 x 0.7 x 20 - 1_B18.3.1M - 4 x 0.7 x 20 Hex SHCS -- 20SHX x 2
扻錪犩 1^Bearing 10x18x5.5
栫櫡譇襜禭Bearing 10x18x5.5
嵑謶獬Bearing 10x18x5.5 x 10
扻錪犩 2^Bearing 10x18x5.5
Äåòàëü5^Óçåë ãàéêè
Ïîäøèïíèê 3õ7õ3^Óçåë ãàéêè x 3
Îñü^Óçåë ãàéêè
Øàéáà^Óçåë ãàéêè

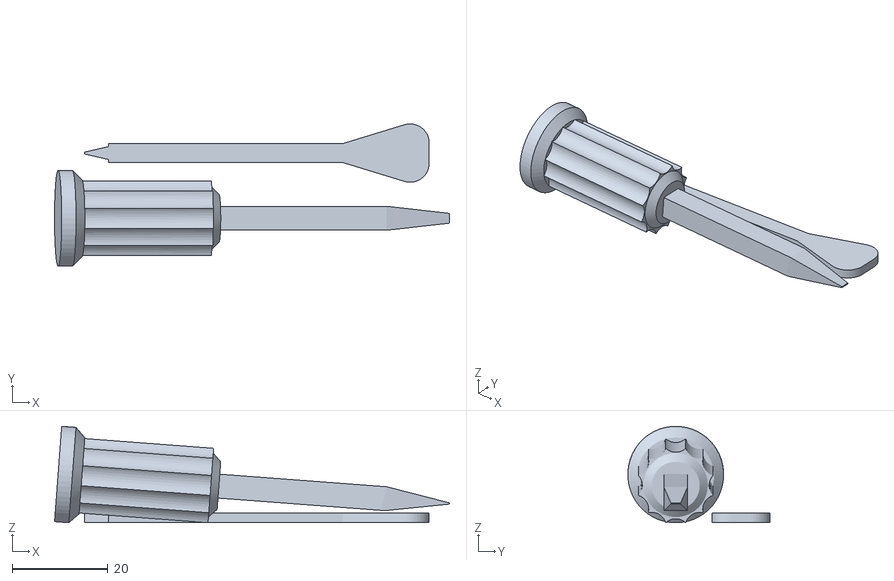
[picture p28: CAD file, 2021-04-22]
Guides/TMC2209/stls/Cacciavite_vref.stl
82.5 x 29.7 x 20.2

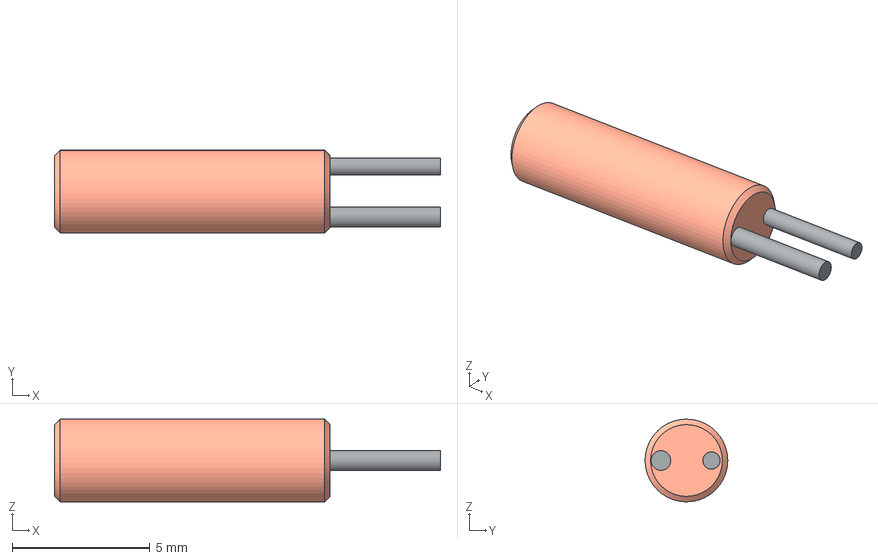
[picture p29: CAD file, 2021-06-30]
Other/FBG5_3D_Model/Flying Bear Ghost 5- STEP format/thermal sensor1.stp
14.0 x 3.00 x 3.00 mm

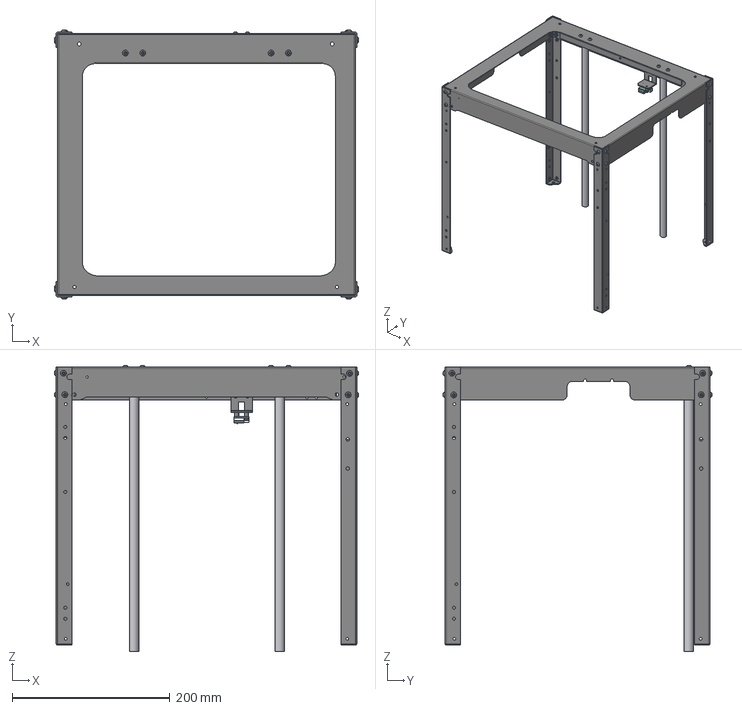
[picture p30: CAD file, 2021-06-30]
Other/FBG5_TopFrame.step
385.9 x 340.9 x 363.5 mm

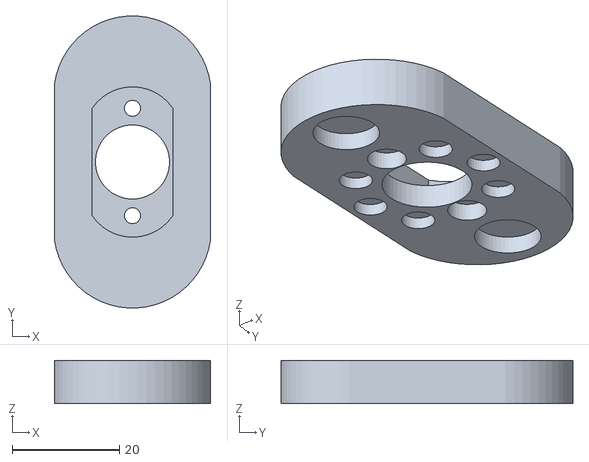
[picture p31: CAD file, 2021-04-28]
Projects/Anti_Wobbling_Flyingbear/1/stls/Bottom_part.stl
29.0 x 54.4 x 8.02

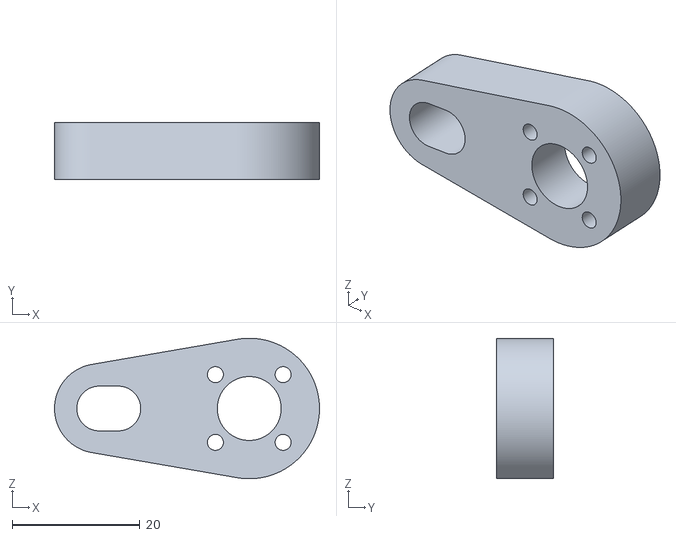
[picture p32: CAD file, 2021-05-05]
Projects/Anti_Wobbling_Flyingbear/2/stls/Dado_staffa.STL
41.5 x 9.00 x 22.0

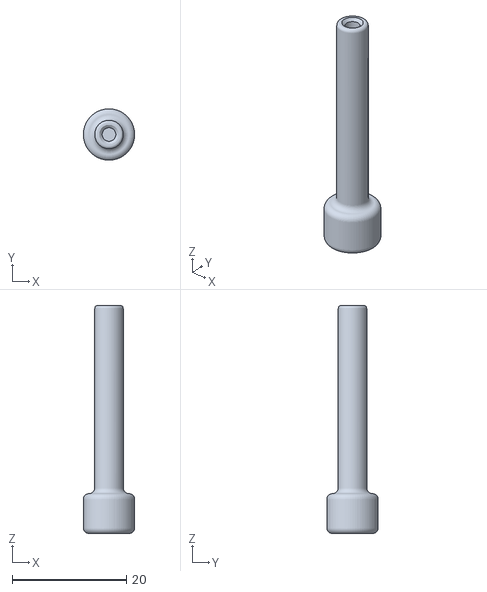
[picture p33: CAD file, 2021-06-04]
Projects/Bed_Leveling/stls/Extender_40.STL
9.00 x 9.00 x 40.0

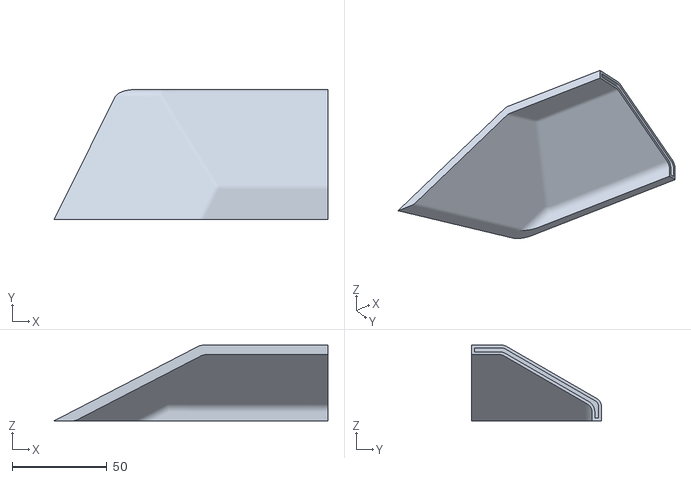
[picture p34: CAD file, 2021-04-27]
Projects/CHUCHATV_Upgrades/1 mechanical fastening/3D PRINT STL and IPT/thermal cover.stl
144.7 x 68.6 x 40.0

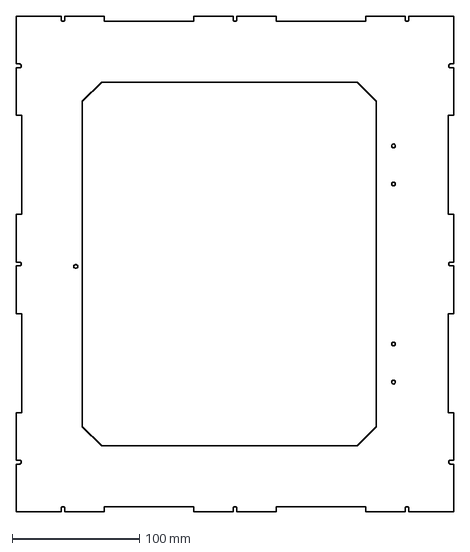
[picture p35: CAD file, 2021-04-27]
Projects/CHUCHATV_Upgrades/1 mechanical fastening/cutting acrylic/Box roof/Box roof DXF.dxf
344.0 x 390.0 mm

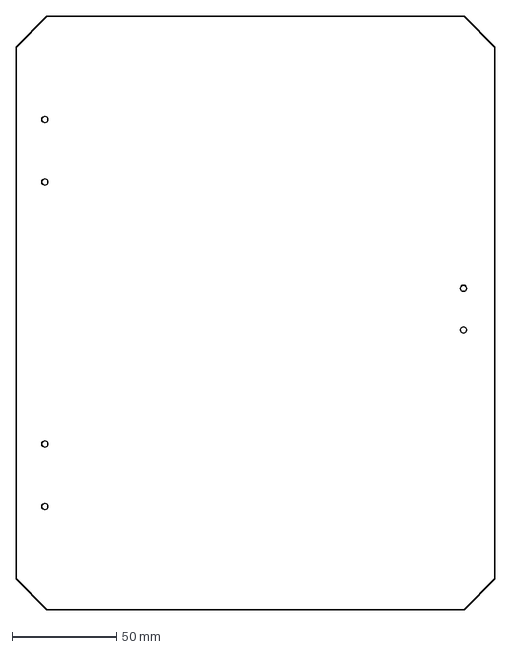
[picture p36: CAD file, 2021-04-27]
Projects/CHUCHATV_Upgrades/1 mechanical fastening/cutting acrylic/Cap/Cap DXF.dxf
230.0 x 285.0 mm

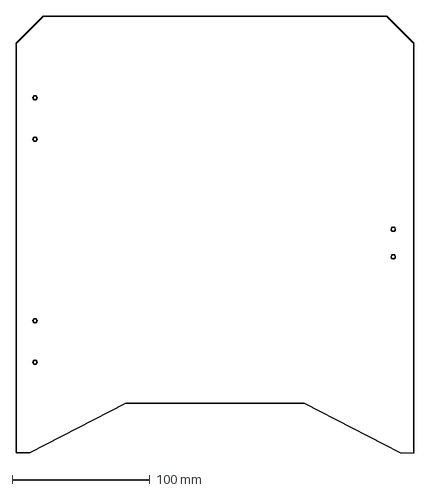
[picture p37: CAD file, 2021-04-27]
Projects/CHUCHATV_Upgrades/1 mechanical fastening/cutting acrylic/Front door/Front door DXF.dxf
289.0 x 317.5 mm

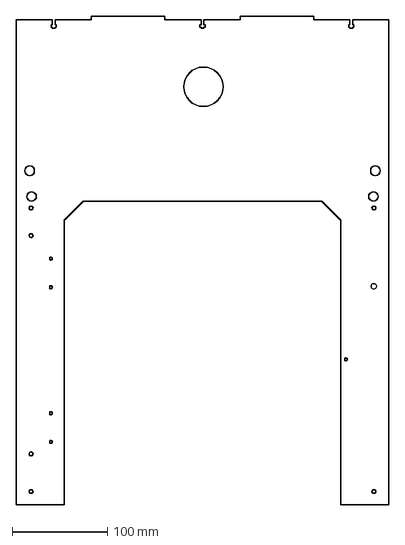
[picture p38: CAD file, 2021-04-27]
Projects/CHUCHATV_Upgrades/1 mechanical fastening/cutting acrylic/Front Panel/Front Panel DXF.dxf
390.0 x 512.0 mm

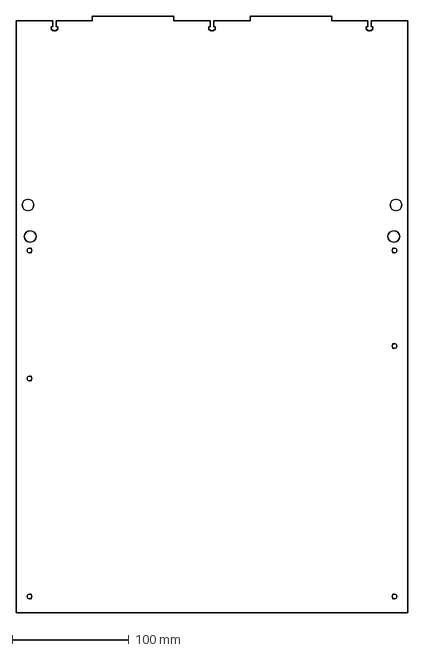
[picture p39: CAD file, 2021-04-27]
Projects/CHUCHATV_Upgrades/1 mechanical fastening/cutting acrylic/Left side panel/Left side panel DXF.dxf
336.0 x 512.0 mm

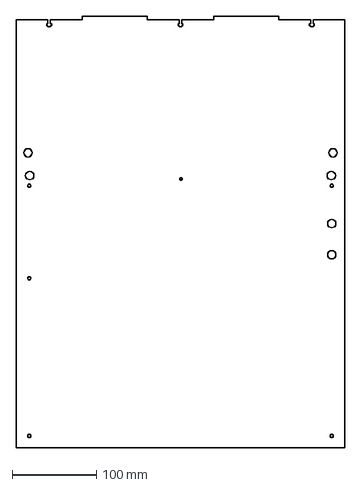
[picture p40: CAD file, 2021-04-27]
Projects/CHUCHATV_Upgrades/1 mechanical fastening/cutting acrylic/Rear panel/Rear panel DXF.dxf
390.0 x 512.0 mm

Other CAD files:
Projects/CHUCHATV_Upgrades/1 mechanical fastening/cutting acrylic/Right side panel/Right side panel DXF.dxf
Projects/CHUCHATV_Upgrades/1 mechanical fastening/Engraving/Front panel LOGO ENGRAVING.dwg
Projects/CHUCHATV_Upgrades/1 mechanical fastening/Fitting drawings/Front panel drawing.dwg
Projects/CHUCHATV_Upgrades/2 NEW E3DV6 STL and IPT/BMG connector for factory.stl
Other/50 Centesimi Carrello Spesa.stl
Other/Cubo_pieno.stl
Other/FBG5_3D_Model/Flying Bear Ghost 5- STEP format/2GT 5mm 0.stp
Other/FBG5_3D_Model/Flying Bear Ghost 5- STEP format/2GT 5mm 2.stp
Other/FBG5_3D_Model/Flying Bear Ghost 5- STEP format/2GT-pulley.stp
Other/FBG5_3D_Model/Flying Bear Ghost 5- STEP format/3010-2.stp
Other/FBG5_3D_Model/Flying Bear Ghost 5- STEP format/3010.stp
Other/FBG5_3D_Model/Flying Bear Ghost 5- STEP format/42-34 motor.stp
Other/FBG5_3D_Model/Flying Bear Ghost 5- STEP format/42-40.stp
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

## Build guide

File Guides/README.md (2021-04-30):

# Guide Utili

## Link a video guide

- [Step/mm estrusore e pid](https://m.youtube.com/watch?v=Tj8GUVdgJkk&feature=youtu.be)
- [Calibrazione flusso](https://youtu.be/tDIeS-q9Qew)

## Guide dettagliate PDF

- [Aggiornamento Firmware](01-Procedura-di-aggiornamento-Firmware.pdf)
- [Calibrazione piano di stampa](02-Calibrazione-Piano-di-Stampa.pdf)
- [Calibrazione Degli Step Estrusore](03-Calibrazione-Degli-Step-Estrusore.pdf)
- [Aumentare la Velocità di Stampa](04-Aumentare-la-Velocità-di-Stampa.pdf)
- [Calibrazione Flusso Stampa](Calibrazione-flusso-Stampa.pdf)
- [Guida Sostituzione TMC220X](Guida-sostituzione-TMC2208.pdf)
- [Link ai video ufficiali Flyingbear](Link-Video-Ufficiali.pdf)
- [Creazione Litofanie](Litofanie.pdf)
- [Sostituzione Ugello e Hotend](Sostituire-ugello-e-hotend.pdf)

## [Sostituzione TMC2209](TMC2209)

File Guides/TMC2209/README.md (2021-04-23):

# Sostituzione Drivers con TMC2209

Per la sostituzione di driver si consiglia l'utilizzo di un giravite ceramico, oppure la stampa di [questo](stls/Cacciavite_vref.stl).

Per una guida dettagliata su come sostituire i driver, guardate [QUI](https://fbghostita.miraheze.org/wiki/Upgrade_a_tmc2209).

## Impostare la VREF

<p align="center">
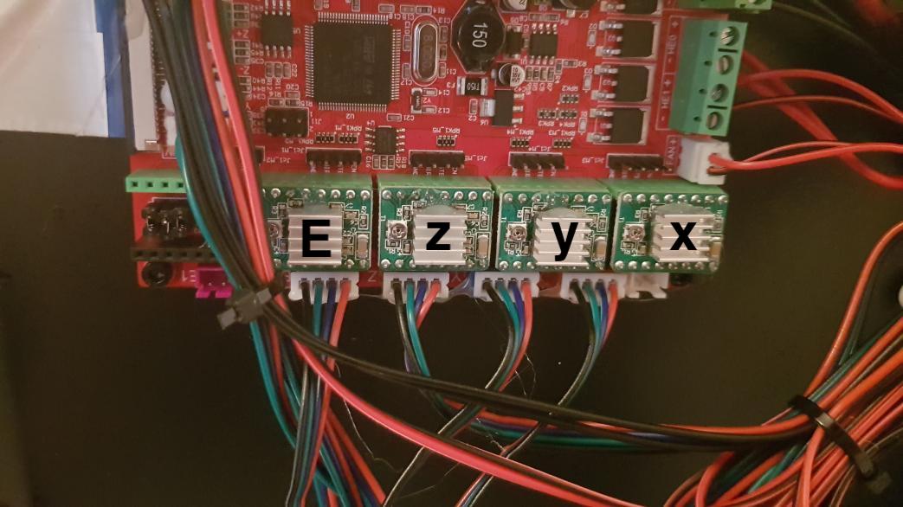
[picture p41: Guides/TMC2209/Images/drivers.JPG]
      
    </p>

### Vecchi valori VREF

- X = 1.23
- Y = 1.28
- Z = 0.96
- E = 1.10

### Nuovi valori VREF impostati per i 4 TMC2209 sostituiti

- X = 0.94
- Y = 0.96
- Z = 0.96
- E = 1.10

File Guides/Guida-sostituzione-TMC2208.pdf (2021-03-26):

SOSTITUZIONE E CALIBRAZIONE STEP LERDGE 2209

Avvertenze: durante la calibrazione della VREF non toccare nessun’altra componente della scheda madre per evitare cortocircuiti.
Link per acquistare i LERDGE, testati ed approvati dalla community (servono quattro driver, tre per gli assi, uno per l'estrusore)
Driver TMC2209 LERDGE (https://a.aliexpress.com/_BPl4HL)
ATTENZIONE: acquistare la versione NON UART (quella senza i piedini trasversali) N.B.
I possessori della Ghost 5 potrebbero accontentarsi di sostituire solo i driver dell'asse Z e dell'estrusore: la Ghost 5 monta di default i 2208 sugli assi X ed Y
Step 1:

Capovolgere su un fianco la stampante e smontare il pannello inferiore per accedere alla parte elettronica.

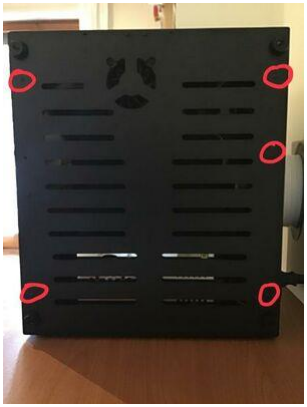
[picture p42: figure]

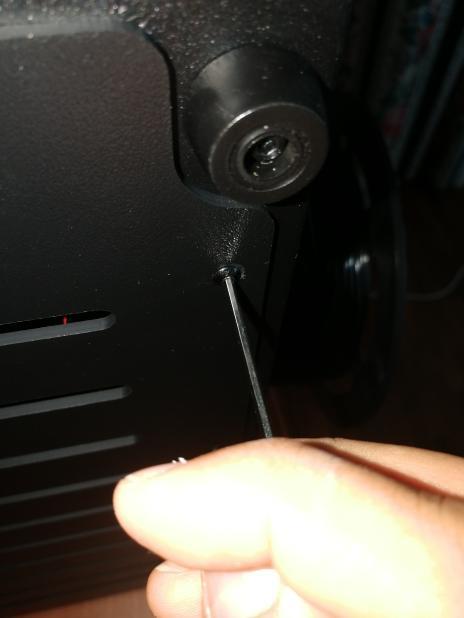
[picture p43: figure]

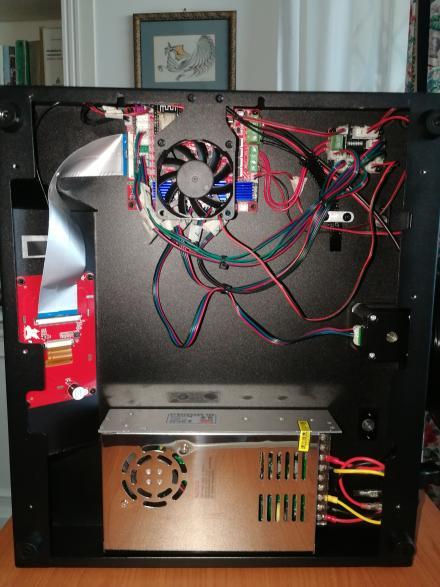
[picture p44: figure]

Step 2:

Smontare la ventola

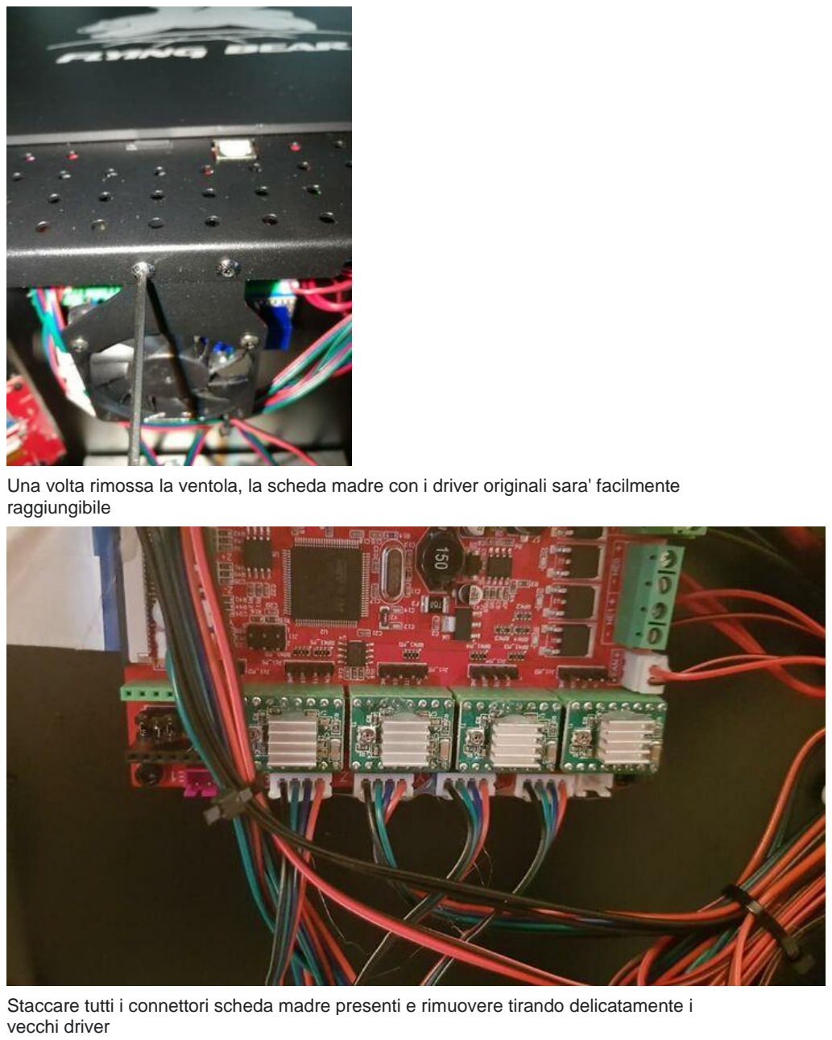
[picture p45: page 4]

Una volta rimossa la ventola, la scheda madre con i driver originali sara' facilmente raggiungibile

Staccare tutti i connettori scheda madre presenti e rimuovere tirando delicatamente i vecchi driver

Step 3:

Inserire i driver, partendo dal lato destro della scheda, uno per volta nei loro slot con la vite in basso a destra.

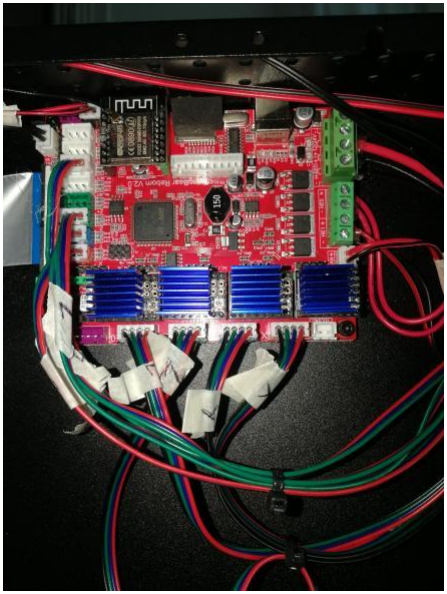
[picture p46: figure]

Accendere la stampante e controllare la VREF usando un multimetro impostato su DC, posizionando il negativo sul pin GND del driver (o dell'alimentazione della scheda)
e il positivo sulla vite, evitando di toccare altre parti del driver

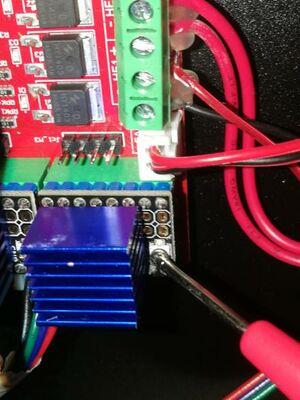
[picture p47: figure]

Il passo successivo sara' regolare la VREF in base al valore rilevato
ATTENZIONE: al momento il valore esatto corretto della VREF è al centro di un dibattito nella community!
ogni stampante è diversa dalle altre, alcuni si sono trovati molto bene con i valori piu' alti, altri hanno riscontrato un surriscaldamento dei motori
Ci sono due versioni:
- X Y Z = 1.2 E0=1.4
- X Y Z = 0.9 E0=1.1
IN ENTRAMBI I CASI NON CI ASSUMIAMO LA RESPONSABILITA’ PER EVENTUALI DANNI ALLA STAMPANTE.
Per regolare la VREF, spegnere la stampante, girare la rotella col cacciavite in dotazione (o quello che avete a disposizione), accendere la stampante e rimisurare.
Ripetere questo passo fino al raggiungimento del valore desiderato della VREF
Step 4:

Estrarre la MicroSD della stampante, inserirla nel computer e salvare sull'hard disk il file robin_nano35_cfg.cur. Rinominarlo in txt (robin_nano35_cfg.txt).
Se non avete questo file potete trovarlo all'interno dello zip originale, presente anche qui nella sezione Firmware
Invertire la direzione dei driver secondo la seguente configurazione:
>INVERT_X_DIR | 0
>INVERT_Y_DIR | 0
>INVERT_Z_DIR | 1

>INVERT_E0_DIR | 1
>INVERT_E1_DIR | 0

Salvare il file e copiarlo sulla MicroSD
Successivamente inserire la SD nella stampante spenta, accendere e aspettare l’aggiornamento
Ecco, finalmente la stampante sara' silenziosissima!

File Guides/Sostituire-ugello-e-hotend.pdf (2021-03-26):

https://www.youtube.com/watch?v=_TwVkbmJz-U&t=344s&ab_channel=FlyingBear3DPrinter

Video Guida su come sostituire il gruppo HotEnd o l’ugello!

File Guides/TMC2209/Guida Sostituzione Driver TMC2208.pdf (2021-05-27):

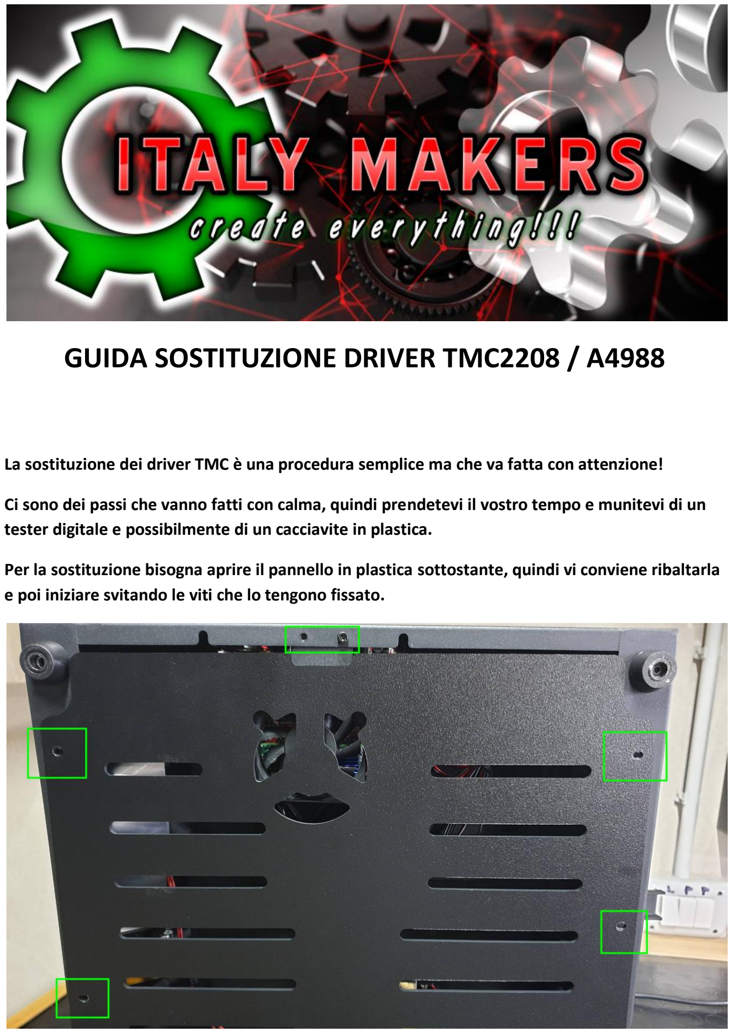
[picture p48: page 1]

## GUIDA SOSTITUZIONE DRIVER TMC2208 / A4988

La sostituzione dei driver TMC è una procedura semplice ma che va fatta con attenzione!

Ci sono dei passi che vanno fatti con calma, quindi prendetevi il vostro tempo e munitevi di un tester digitale e possibilmente di un cacciavite in plastica.

Per la sostituzione bisogna aprire il pannello in plastica sottostante, quindi vi conviene ribaltarla e poi iniziare svitando le viti che lo tengono fissato.

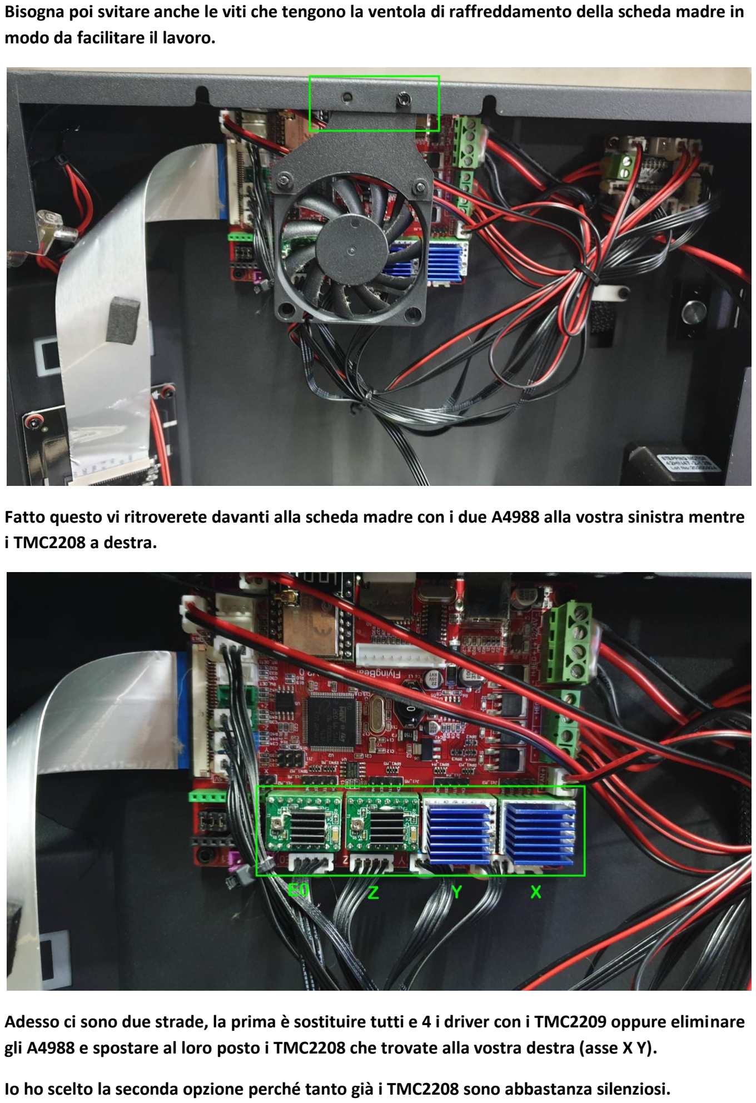
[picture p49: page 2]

Bisogna poi svitare anche le viti che tengono la ventola di raffreddamento della scheda madre in modo da facilitare il lavoro.

Fatto questo vi ritroverete davanti alla scheda madre con i due A4988 alla vostra sinistra mentre i TMC2208 a destra.

Adesso ci sono due strade, la prima è sostituire tutti e 4 i driver con i TMC2209 oppure eliminare gli A4988 e spostare al loro posto i TMC2208 che trovate alla vostra destra (asse X Y).

Io ho scelto la seconda opzione perché tanto già i TMC2208 sono abbastanza silenziosi.

A questo punto munirsi di tester digitale e impostarlo su 20V come fondo scala.

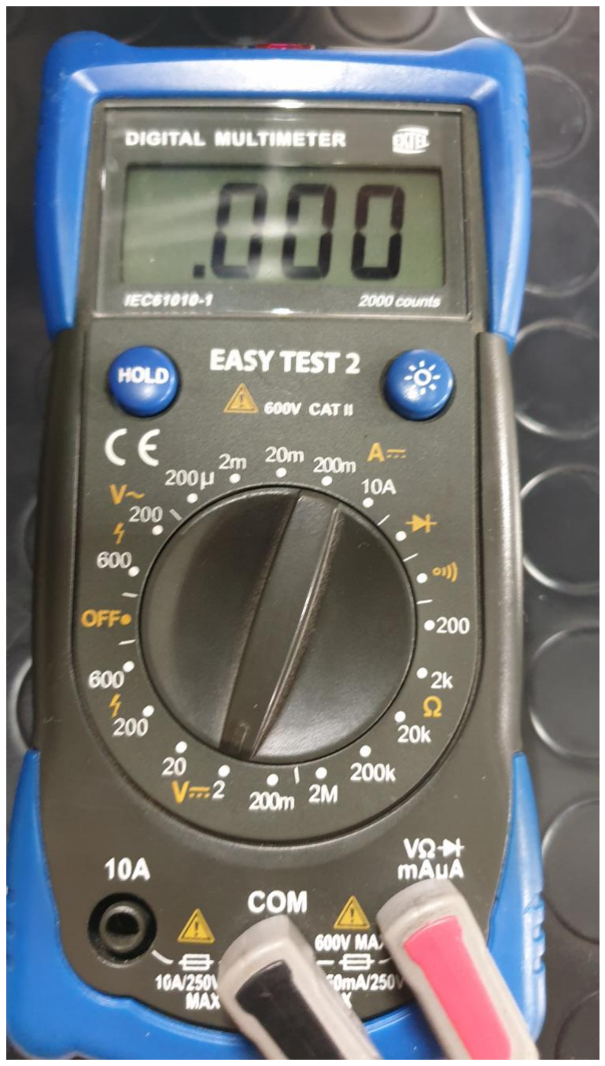
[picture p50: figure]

Mettere il puntale del GND (NERO) sul negativo dell’alimentatore della stampante o comunque su qualsiasi punto GND e il puntale del positivo (ROSSO) al centro del trimmer del DRIVER TMC da misurare.

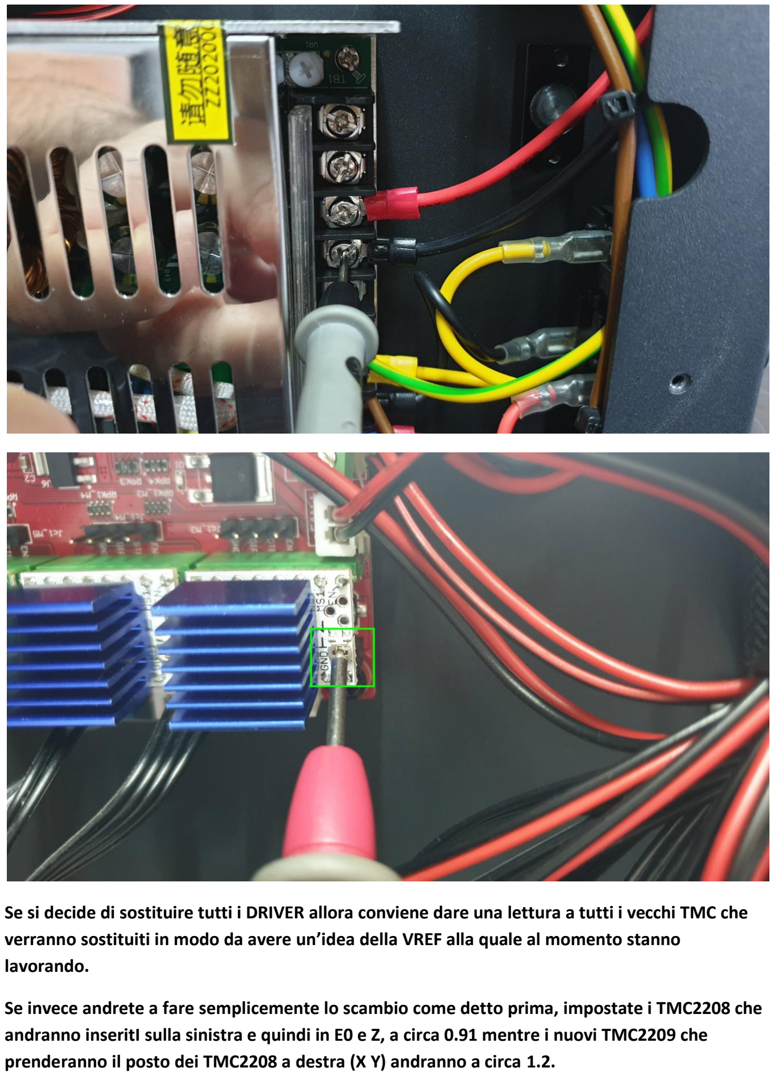
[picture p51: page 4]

Se si decide di sostituire tutti i DRIVER allora conviene dare una lettura a tutti i vecchi TMC che verranno sostituiti in modo da avere un’idea della VREF alla quale al momento stanno lavorando.

Se invece andrete a fare semplicemente lo scambio come detto prima, impostate i TMC2208 che andranno inseritI sulla sinistra e quindi in E0 e Z, a circa 0.91 mentre i nuovi TMC2209 che prenderanno il posto dei TMC2208 a destra (X Y) andranno a circa 1.2.

Se non avete un cacciavite in plastica, dovrete leggere la tensione a stampante accesa cercando con i puntali del tester di non toccare altro che i punti indicati prima, leggere la tensione e poi spegnere la stampante, ruotare il trimmer. Riaccendere la stampante e rileggere la tensione fin quando non otterrete il voltaggio corretto!

Mi raccomando, è un operazione da fare con calma, senza correre e bisogna essere il più precisi possibili.

Fatto questo, bisogna incollare su tutti e 4 i TMC i dissipatori forniti, rimanendo attenti che la parte metallica non vada a toccare i pin!!!

Bene, adesso passiamo al firmware…

Scaricate il firmware, aprite la cartella una volta averlo scompattato e prendete il file robin_nano35_cfg.txt, apritelo e recatevi nella sezione dedicata alla direzione dei drivere!

#============================== ²½½øµç»úÉèÖÃ ============================

#µç»ú·½ÏòÅäÖÃ.

>INVERT_X_DIR | 0
>INVERT_Y_DIR | 0
>INVERT_Z_DIR | 0
>INVERT_E0_DIR | 0
>INVERT_E1_DIR | 0

Invertite il senso di direzione di E0 e Z METTENDOCI 1 al posto dello 0.

Ovviamente se cambiate tutti e 4 i driver con i TMC2209 l’inversione andrà fatta per tutti.

Bene, salvate il tutto e mettete il file robin_nano35_cfg.txt nella scheda SD formattata, a stampante spenta, inserite la schedina e poi accendete.

Avete finito, se non avrete fatto danni e tutto sarà andato a buon fine la stampante sarà più silenziosa e precisa, almeno sugli assi X Y.

NB.

SE IN CORSO DI STAMPA, NOTATE UN SURRISCALDAMENTO ECCESSIVO DEI MOTORI, VORRA’ DIRE CHE DOVRETE ABBASSARE LA VREF PER NON DANNEGGIARE I MOTORI.

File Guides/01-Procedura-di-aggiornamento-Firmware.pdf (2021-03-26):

## Procedura di aggiornamento

- Scarica il file compresso del firmware;
- Estrai il file appena scaricato;
- Collega la microSD della stampante al PC/Mac;
- Fai un backup dei file contenuti sulla microSD della stampante;
- Copia l'intero contenuto (file e cartelle) all'interno della microSD;
- Opzionale: Se in passato hai effettuato delle modifiche al file di configurazione "robin_nano35_cfg.txt", ricorda di inserire le stesse nel nuovo file, con lo stesso nome, che troverai nella cartella del nuovo firmware;
- Spegni la stampante (se accesa);
- Inserisci la microSD nella stampante;
- Riaccendi la stampante;
- Attendi il caricamento del nuovo firmware;
- Concluso l'aggiornamento sullo schermo della stampante visualizzerai il menu iniziale.

Attenzione: non spegnere per nessun motivo la stampate durante la procedura di aggiornamento.

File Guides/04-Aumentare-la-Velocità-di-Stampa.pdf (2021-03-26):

## Aumentare la velocita' di stampa

Il firmware stock limita la velocita' della stampante, che puo' raggiungere accelerazioni piu' elevate.

Questa limitazione e' la causa principale della discrepanza tra i tempi stimati da cura e quelli effettivi di stampa.

Per rimuovere le limitazioni, sostituire i seguenti valori nel robin_nano_cgf.txt

Attenzione, non fate un copia e incolla ma modificate direttamente i valori manualmente e solo quelli indicati!!!

>DEFAULT_X_MAX_FEEDRATE | 300 | #XÖáÄ¬ÈÏËÙ¶È (mm/s)
>DEFAULT_Y_MAX_FEEDRATE | 300 | #YÖáÄ¬ÈÏËÙ¶È (mm/s)
>DEFAULT_Z_MAX_FEEDRATE | 5 | #ZÖáÄ¬ÈÏËÙ¶È (mm/s)
>DEFAULT_E0_MAX_FEEDRATE | 100 | #EÖáÄ¬ÈÏËÙ¶È (mm/s)
>DEFAULT_E1_MAX_FEEDRATE | 70 | #EÖáÄ¬ÈÏËÙ¶È (mm/s)
>DEFAULT_X_MAX_ACCELERATION | 1000 | #XÖáÄ¬ÈÏ×î´ó¼ÓËÙ¶È (change/s) change
= mm/s
>DEFAULT_Y_MAX_ACCELERATION | 1000 | #YÖáÄ¬ÈÏ×î´ó¼ÓËÙ¶È (change/s) change
= mm/s
>DEFAULT_Z_MAX_ACCELERATION | 200 | #ZÖáÄ¬ÈÏ×î´ó¼ÓËÙ¶È (change/s) change =
mm/s
>DEFAULT_E0_MAX_ACCELERATION | 80000 | #EÖáÄ¬ÈÏ×î´ó¼ÓËÙ¶È (change/s)
change = mm/s
>DEFAULT_E1_MAX_ACCELERATION | 1000 | #EÖáÄ¬ÈÏ×î´ó¼ÓËÙ¶È (change/s) change
= mm/s
>DEFAULT_ACCELERATION | 1000 | #X,Y,Z,E ´òÓ¡Ê±µÄÄ¬ÈÏ¼ÓËÙ¶È
>DEFAULT_RETRACT_ACCELERATION | 3000 | #X,Y,Z,E »Ø³éÄ¬ÈÏ¼ÓËÙ¶È
>DEFAULT_TRAVEL_ACCELERATION | 1000 | #X,Y,Z ·Ç´òÓ¡Ê±µÄÄ¬ÈÏ¼ÓËÙ¶È
>DEFAULT_MINIMUMFEEDRATE | 0.0 | #Ä¬ÈÏ×îÐ¡ËÙ¶È
>DEFAULT_MINSEGMENTTIME | 20000
#»º´æ¿ÕÊ±£¬Ò»¸öÒÆ¶¯ËùÐèµÄ×îÐ¡Ê±¼ä(µ¥Î»ms).

>DEFAULT_MINTRAVELFEEDRATE | 0.0 | #

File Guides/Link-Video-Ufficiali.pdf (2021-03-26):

https://www.youtube.com/channel/UCO9d2eNVwLAmIJnQt6TsNKw/videos

Link ai Video Ufficiali di FlyingBear.

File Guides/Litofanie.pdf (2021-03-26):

https://3dp.rocks/lithophane/?fbclid=IwAR2Xbj2uO9yvc7OuCpI0HoDyXCiKk3XxMTbsRrHPCtOElBaGIOLaFqJTTY (https://3dp.rocks/lithophane/?fbclid=IwAR2Xbj2uO9yvc7OuCpI0HoD-yXCiKk3XxMTbsRrHPCtOElBaGIOLaFqJTTY)

https://www.youtube.com/watch?v=tdVxMzpPAvw&t=427s&ab_channel=AlbertoFerrarino

Vi lascio i collegamenti al Video su YouTube e al sito per realizzare le vostre Litofanie!

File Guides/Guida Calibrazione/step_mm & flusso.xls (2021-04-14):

Calcolo Step/mm
Step EEPROM | mm Campione | mm Realmente Ottenuti
80 | 40.00 | 40.00
Nuovi Step
80.00
Calcolo Flusso
Flusso iniziale | Spessore Parete Impostato | Spessore Parete Misurato | Nuovo Valore di Flusso | Valore di Flusso Primo Layer
100.00 | 0.45 | 0.46 | 97.83 | 102.22

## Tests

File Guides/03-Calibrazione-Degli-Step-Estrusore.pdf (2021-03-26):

# Calibrazione degli step

## Estrusore

In questo caso, è necessario l'utilizzo di Repetier Host.

Allego il video su YouTube in modo da essere più semplice!

https://www.youtube.com/watch?v=Tj8GUVdgJkk&list=LL&index=22&t=144s&ab_channel=BrunoLasca ro

Adesso che tutto è pronto lato software, andiamo a vedere cosa fare con l'hardware.

Il primo passo da fare è estrarre il filamento dall'ugello, se presente. Far ritirare il filo completamente.

Una volta rimosso il filamento, estrarre il tubo di teflon dall'estrusore, rimuovendo la fascetta (se presente) e premendo verso il pezzo di plastica del connettore.

Ricaricare il filamento, stavolta fino a quando non esce appena dall'estrusore. Con le tronchesi, tagliare il filamento a filo con il connettore.

A questo punto, inviare, tramite RH, i seguenti comandi GCode:

M302 P1; Disabilita la protezione termale dell'estrusore
G92 E0; Riposiziona l'origine dell'estrusore nella posizione attuale G1 E280 F800; Estrude 280 mm di filamento

Adesso bisogna misurare la lunghezza del filamento estruso. Prendere un righello, misurare la lunghezza del filamento

Adesso calcolare gli step reali con la seguente formula:

400 * (280/x) ==> x = lunghezza misurata

400 è il numero di step di default

Se, per esempio, avessimo misurato 265, la formula qui sopra sarebbe:

400 * (280/265)

Una volta calcolato il nuovo valore, inserirlo nel file robin_nano35_cfg.txt.

Cercare:

DEFAULT_E0_STEPS_PER_UNIT

Sostituire il valore di default con il valore ottenuto dalla formula.

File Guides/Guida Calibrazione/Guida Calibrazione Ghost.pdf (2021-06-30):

Hai appena assemblato la tua nuova stampante e sei pronto per stampare…bene prima però va tarata a dovere per ottenere stampe di qualità estetica e dimensionale.

Ora ti spiegherò passo passo cosa fare.

Materiale necessario per la taratura: Calibro con almeno 2 decimali, foglio A4, pennarello ALLINEAMENTO PIATTO DI STAMPA

Se la tua stampante ha un sistema di livellamento del piatto automatico tipo BLTouch passa alla prossima sezione. Prendendo in considerazione che la tua stampante abbia un livellamento del piatto manuale procediamo come segue:

Fai la home degli assi
Porta la stampante a temperatura di stampa (200° estrusore 60° bed)
Ed esegui la procedura di livellamento del piatto
Inserisci il foglio tra piatto e ugello e regola le ruote in modo da sentire la frizione tra ugello e foglio.

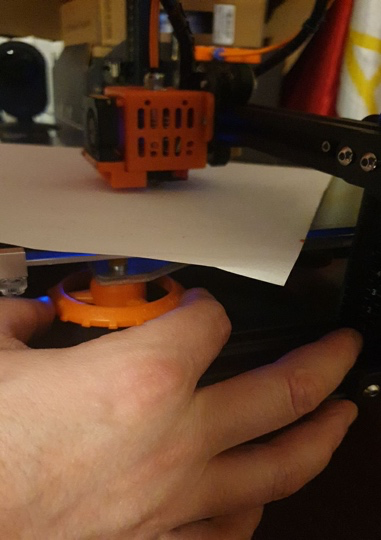
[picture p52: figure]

Fatto questo per tutto il piatto l’operazione è completata.

TARATURA ESTRUSORE

Essere sicuri che la tua stampante stia esattamente estrudendo la quantità di filamento richiesto è di fondamentale importanza per evitare problemi sovraestrusione o sottoestrusione.

Vediamo come fare:

Rimuovi il tubo PTFE dall’estrusore premendo la parte in plastica del raccordo e inserisci il filamento fino alla plastica del raccordo

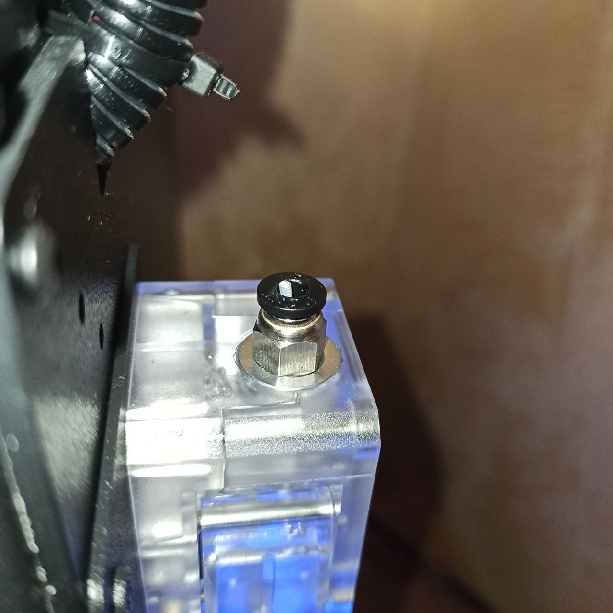
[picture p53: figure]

Scarica il programma Repetier Host

Ora collega la stampante al PC con il cavo USB in dotazione e collegala a Repetier host seguendo questa guida.

Ora che è collegata alla voce controlli manuali, gcode, invia i seguenti codici

M302 P1
G91
G1 E150 F1000

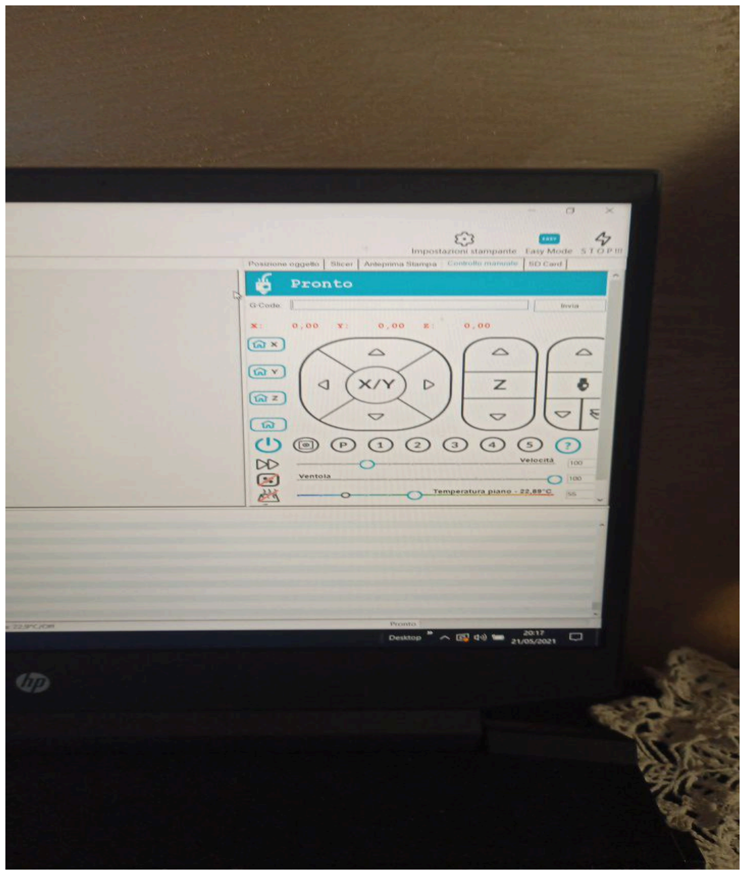
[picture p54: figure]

A questo punto la stampante comincerà a far uscire il filamento

Adesso si aprono 2 strade:

1) Il tuo segmento di filo è lungo esattamente 150mm. Calibrazione finita passa alla prossima.
2) Il tuo segno non è lungo 150mm

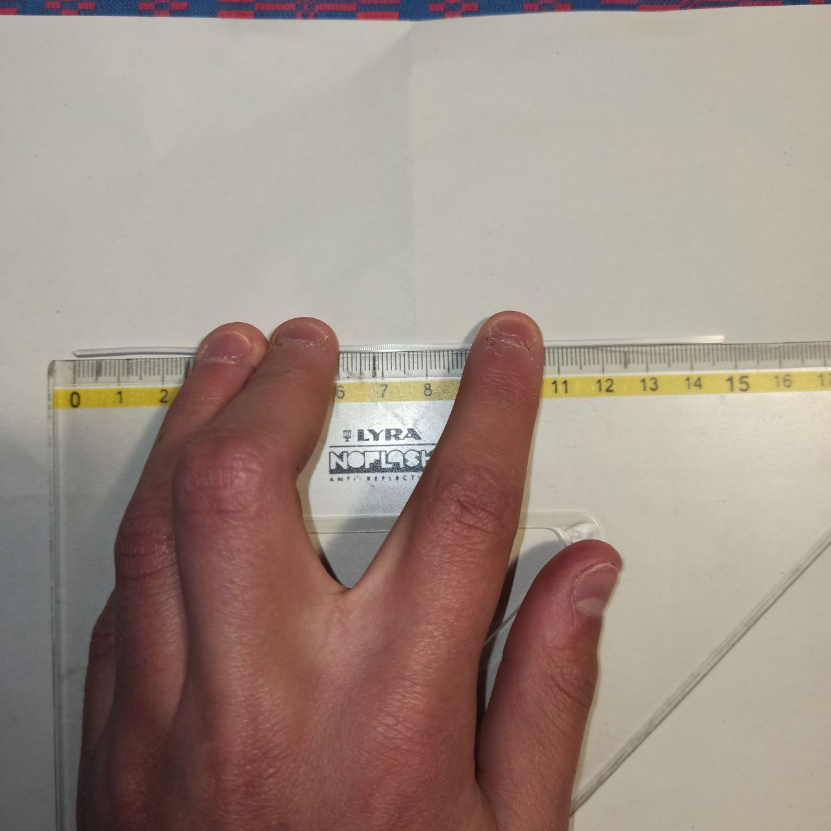
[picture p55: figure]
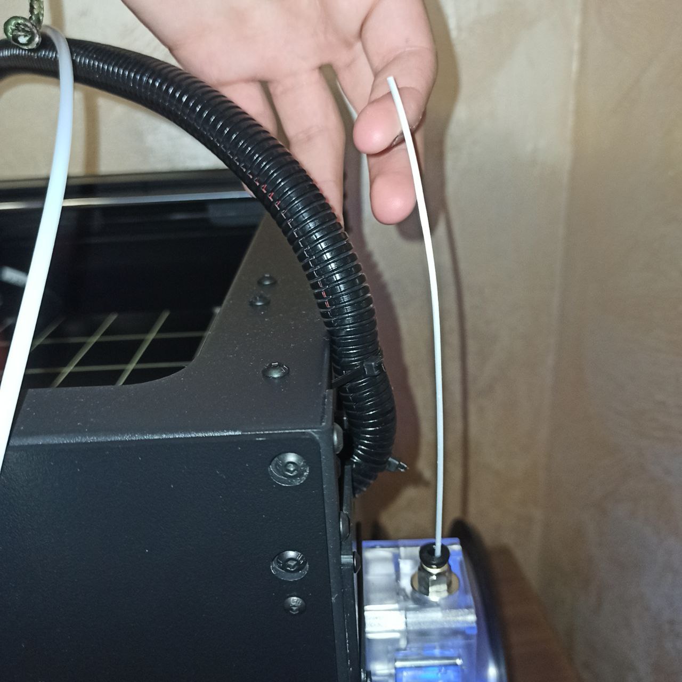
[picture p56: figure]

Bene, misura la distanza col calibro tra il punto 0 (plastica del raccordo) e il punto massimo del filamento (cerca di essere il più preciso possibile in questa misurazione) Ora calcola i nuovi step/mm dell’estrusore tramite il foglio Excel step_mm & flusso.xls oppure secondo la seguente formula.

(Valore Teorico / Valore Reale) * Step programmati

Per Sapere il numero degli Step programmati di default li trovi mandando alla stampante il gcode M503. In generale in condizioni stock sono X80 Y80 Z400 E400

Es.

mm teorici 150

mm estrusi 147

step 400

(150/147)*400= 408.16 circa

Dato che la macchina accetta un solo decimale il nuovo valore di step da memorizzare sarà 408.2

Per inserire gli step invia il gcode M92 E408.2

Memorizza il dato inserito con M500

Verifica il corretto inserimento del dato con M503

M302 P0 per abilitare nuovamente la protezione cold extrusion

Ripeti I’operazione e a questo punto estruderai perfettamente 150mm.
Arrivato a questo punto rimetti i tubo ptfe al suo posto, inserisci il filamento correttamente e ripeti l’operazione appena descritta stavolta però estrudendo il materiale come se dovessi stampare. Misura col calibro 150mm di filo (Per questa operazione ti suggerisco di togliere il sensore di filamento inserendo un pezzo di filo all’interno).

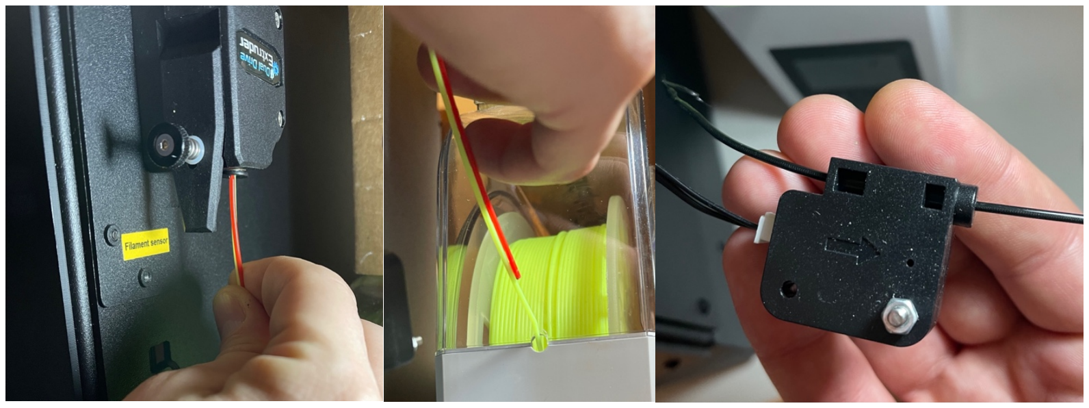
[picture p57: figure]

Scalda l’ugello a 200°
G91
G1 E150 F200
Il segno del pennarello DEVE arrivare sotto all’estrusore dove è stato preso lo 0. Se così non fosse controllare la pressione della molla ed eventualmente se il nozzle è libero da impedimenti.

TARATURA FLUSSO

Per il flusso la taratura è molto semplice ma va ripetuta per tutti i materiali(PLA,PETG,TPU…), ugelli (materiale, diametro) e per tutti gli slicer che hai intenzione di usare.

Scarica da Thingiverse il cubo per la calibrazione.

Prendiamo ad esempio lo Slicer Cura e materiale PLA

Importiamo nello slicer il cubo appena scaricato

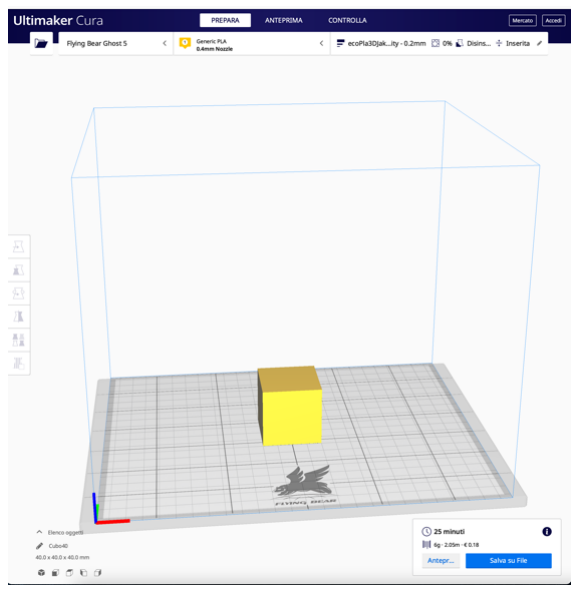
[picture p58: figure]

e settiamo la stampa come segue:

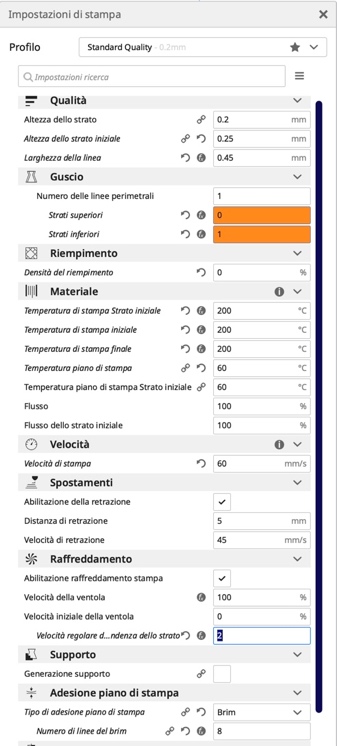
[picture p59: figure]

Ora la nostra anteprima sarà questa

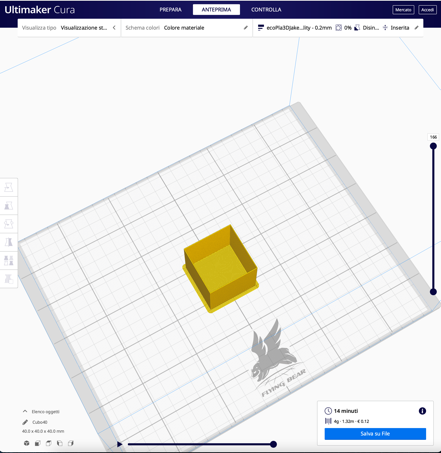
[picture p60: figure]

N.B. La distanza di retrazione va regolata a seconda della tipologia di estrusore:

Se Bowden 5/7mm

Se Direct 2/3mm

Salviamo il file gcode nella memory card e andiamo in stampa.

Abbiamo finalmente ottenuto il nostro primo cubo

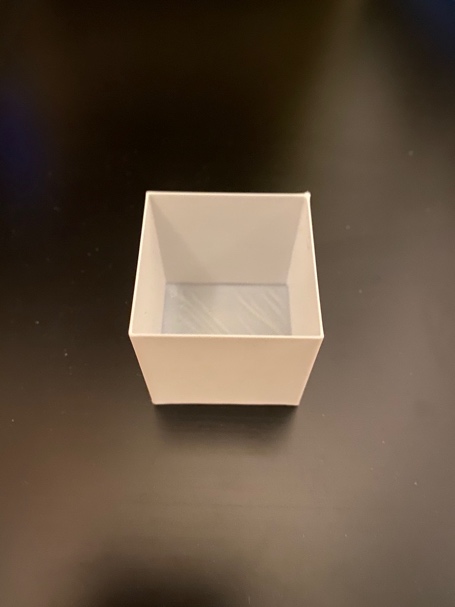
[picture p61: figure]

Dal quale possiamo ottenere diverse informazioni.

Verifica della distanza tra piatto e ugello


Una lettura in linea di massima delle dimensioni esterne (le vedremo meglio al paragrafo successivo)


Ma soprattutto lo spessore della parete che sappiamo aver impostato a 0.45mm su Cura.

A questo punto col nostro fidato calibro verifichiamo che le 4 pareti siano esattamente 0.45mm.


Se così non fosse ovviamente basta applicare la formula o sempre tramite il foglio Excel step_mm & flusso.xls
(spessore teorico / spessore ottenuto)*100

per arrivare ad avere il corretto valore di flusso da mettere nello slicer.

IEs: (0.45/0.52)*100= 86.5

nseriamo i valori richiesti e calcoliamo i nuovi valori di Flusso.

Basterà dunque aggiornare il dato di flusso su Cura

esportare il nuovo gcode e rilanciare la stampa per la verifica. Otterremo così un nuovo cubo dello spessore voluto.


TARATURA ASSE X,Y,Z

Siamo giunti finalmente all’ultima taratura base per la nostra nuova stampante. Ora stampiamo un ultimo cubo che ci serve per valutare l’accuratezza dimensionale.

In Cura dovremmo avere ancora il nostro cubo usato per la regolazione del flusso in caso contrario importiamolo di nuovo.

Settiamo Cura come segue:


Ora la nostra anteprima sarà così:


Salviamo di nuovo tutto su SD e mandiamo in stampa.

Risultato:


Prima di staccare il cubo dal piatto ricordiamoci di segnare con un pennarello la posizione dell’asse X e Y ricordando che l’asse X si trova di fronte e l’asse Y sul fianco. Una volta freddo e staccato dal piano torniamo a misurare col calibro le dimensioni del cubo al centro della parete cercando di evitare eventuali deformazioni dovute al brim o altri difetti.


Sempre tramite il foglio Excel step_mm & flusso.xls inseriamo i valori richiesti e calcoliamo i nuovi step.

Gcode da inviare per settare gli step

M92 X”valore” Y”valore” Z”valore”
Es:
M92 X80 Y80 Z400
M500 per salvare
M503 per verificare il corretto inserimento

Ora rimandiamo in stampa lo stesso cubo stampato in precedenza ed otterremo un nuovo cubo delle misure esatte.


Le Calibrazioni base sono terminate.

Ora non resta che determinare la corretta temperatura di stampa per il vostro filamento con una Temp Tower e una stampa di verifica generale con una 3DBenchy.

Buone Stampe

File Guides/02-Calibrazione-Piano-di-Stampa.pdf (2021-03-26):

# Calibrazione del piano di stampa

La calibrazione del piano di stampa rientra nelle calibrazioni essenziali da effettuare. Inizialmente può sembrare una procedura complicata ma con questi semplici passi potrai ottenere una calibrazione semplice ed efficiente.

1) Chiudere (stringere) le 4 molle del piano a fine corsa:

•

2) Regolare la vite di fine corsa del piano "Z" in modo tale da ottenere uno spazio tra punta e ugello di 2mm. Tips and tricks: Come misura di riferimento puoi usare la brugola in dotazione, la seconda più piccola:

•

Regolazione asse "Z"

•

Misurazione dei 2mm di distanza

•

Misurazione della brugola
3) Iniziare usando la funzione "leveling" della stampante:

•

•

4) Usare il foglio in dotazione o un foglio A4 per calibrare tutti e 4 i punti. Tra ugello e foglio dev'essere presente un leggero attrito:

•

•

Il foglio in dotazione

## I consigli per una buona calibrazione

- Riscaldare il piano a 60°C durante tutto il processo di calibrazione;
- Ripetere la calibrazione 4/5 volte;
- Tra una calibrazione e l’altra portare tutti gli assi in "home";
- Pulire il piano di stampa con alcool isopropilico.

https://www.youtube.com/channel/UCO9d2eNVwLAmIJnQt6TsNKw/videos

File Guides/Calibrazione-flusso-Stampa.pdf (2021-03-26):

https://www.youtube.com/watch?v=tDIeS-q9Qew&list=LL&index=7&t=191s&ab_channel=MicheleDicati

Vi lascio il link al video YouTube di come effettuare la calibrazione del flusso di stampa!!!

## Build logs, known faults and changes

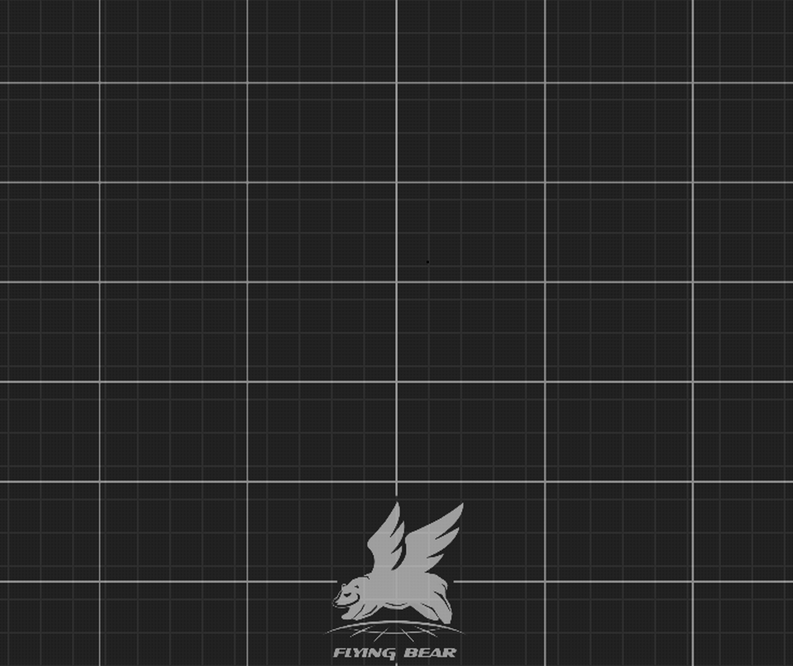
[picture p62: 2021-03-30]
Slicers/PrusaSlicer/Flyingbear_Bed/FlyingBear_G5_bed_FIX.png

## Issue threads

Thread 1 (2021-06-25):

When G28 is executed, Z_SAFE_HOMING is not working Ghost 5

pure100kim, 2021-06-25:
Ghost 5 main board is Robin nano S.

I installed 3D touch.
G29 auto leveling is normal operation.

But When G28 is executed, 3Dtouch does not move to the center of the HOTBED.
Z-axis leveling at X0, Y0 point.

How does it work Z_SAFE_HOMING?

It was applied to the CFG file as below.

#============================= Z Probe Options =============================
#Probe interface Z-Min
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

>Z_SAFE_HOMING 1 # 0:Do not enable, 1: enable

#=============================== Bed Leveling ==============================

>BED_LEVELING_METHOD 3 # 0:NULL_BED_LEVELING; 3:AUTO_BED_LEVELING_BILINEAR; 5:MESH_BED_LEVELING

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

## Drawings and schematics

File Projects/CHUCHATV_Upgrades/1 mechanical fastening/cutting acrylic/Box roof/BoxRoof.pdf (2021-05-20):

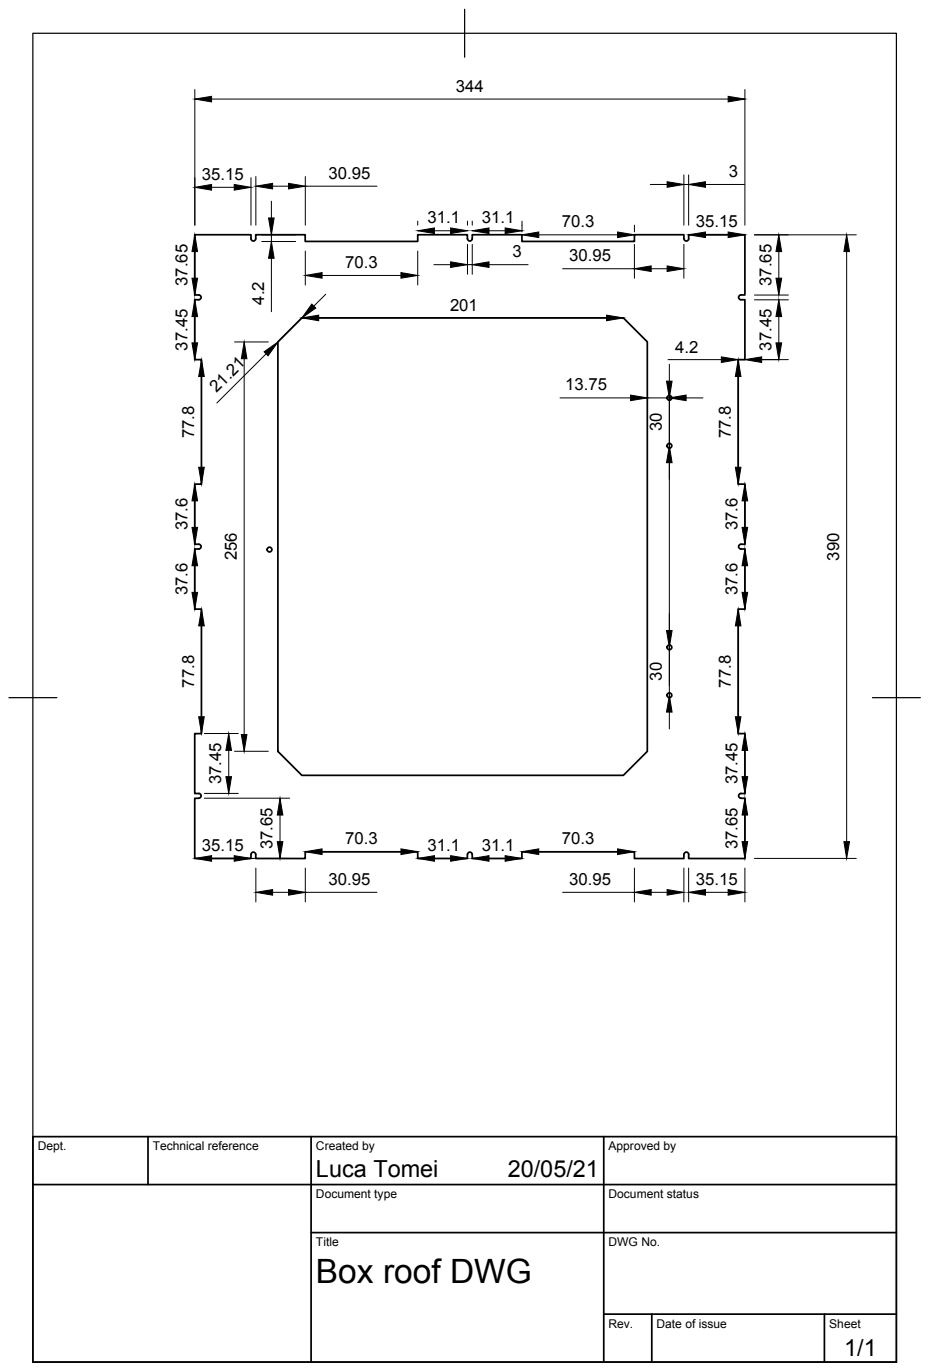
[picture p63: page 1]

Dept. | Technical reference | Created by Luca Tomei 20/05/21 | Approved by

Document type | Document status

Title Box roof DWG | DWG No.

Rev. | Date of issue | Sheet 1/1

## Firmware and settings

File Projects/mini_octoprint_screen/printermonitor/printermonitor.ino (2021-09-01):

/** The MIT License (MIT)

Copyright (c) 2018 David Payne

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
THE SOFTWARE IS PROVIDED "AS IS", WITHOUT WARRANTY OF ANY KIND, EXPRESS OR
IMPLIED, INCLUDING BUT NOT LIMITED TO THE WARRANTIES OF MERCHANTABILITY,
FITNESS FOR A PARTICULAR PURPOSE AND NONINFRINGEMENT. IN NO EVENT SHALL THE
AUTHORS OR COPYRIGHT HOLDERS BE LIABLE FOR ANY CLAIM, DAMAGES OR OTHER
LIABILITY, WHETHER IN AN ACTION OF CONTRACT, TORT OR OTHERWISE, ARISING FROM,
OUT OF OR IN CONNECTION WITH THE SOFTWARE OR THE USE OR OTHER DEALINGS IN THE
SOFTWARE.
*/

// Additional Contributions:
/* 15 Jan 2019 : Owen Carter : Add psucontrol option and processing */

 /**********************************************
 * Edit Settings.h for personalization
 ***********************************************/

#include "Settings.h"

#define VERSION "2.5"

#define HOSTNAME "OctMon-" 
#define CONFIG "/conf.txt"

/* Useful Constants */
#define SECS_PER_MIN  (60UL)
#define SECS_PER_HOUR (3600UL)

/* Useful Macros for getting elapsed time */
#define numberOfSeconds(_time_) (_time_ % SECS_PER_MIN)  
#define numberOfMinutes(_time_) ((_time_ / SECS_PER_MIN) % SECS_PER_MIN) 
#define numberOfHours(_time_) (_time_ / SECS_PER_HOUR)

// Initialize the oled display for I2C_DISPLAY_ADDRESS
// SDA_PIN and SCL_PIN
#if defined(DISPLAY_SH1106)
  SH1106Wire     display(I2C_DISPLAY_ADDRESS, SDA_PIN, SCL_PIN);
#else
  SSD1306Wire     display(I2C_DISPLAY_ADDRESS, SDA_PIN, SCL_PIN); // this is the default
#endif

OLEDDisplayUi   ui( &display );

void drawProgress(OLEDDisplay *display, int percentage, String label);
void drawOtaProgress(unsigned int, unsigned int);
void drawScreen1(OLEDDisplay *display, OLEDDisplayUiState* state, int16_t x, int16_t y);
void drawScreen2(OLEDDisplay *display, OLEDDisplayUiState* state, int16_t x, int16_t y);
void drawScreen3(OLEDDisplay *display, OLEDDisplayUiState* state, int16_t x, int16_t y);
void drawHeaderOverlay(OLEDDisplay *display, OLEDDisplayUiState* state);
void drawClock(OLEDDisplay *display, OLEDDisplayUiState* state, int16_t x, int16_t y);
void drawWeather(OLEDDisplay *display, OLEDDisplayUiState* state, int16_t x, int16_t y);
void drawClockHeaderOverlay(OLEDDisplay *display, OLEDDisplayUiState* state);

// Set the number of Frames supported
const int numberOfFrames = 3;
FrameCallback frames[numberOfFrames];
FrameCallback clockFrame[2];
boolean isClockOn = false;

OverlayCallback overlays[] = { drawHeaderOverlay };
OverlayCallback clockOverlay[] = { drawClockHeaderOverlay };
int numberOfOverlays = 1;

// Time 
TimeClient timeClient(UtcOffset);
long lastEpoch = 0;
long firstEpoch = 0;
long displayOffEpoch = 0;
String lastMinute = "xx";
String lastSecond = "xx";
String lastReportStatus = "";
boolean displayOn = true;

// OctoPrint Client
OctoPrintClient printerClient(OctoPrintApiKey, OctoPrintServer, OctoPrintPort, OctoAuthUser, OctoAuthPass, HAS_PSU);
int printerCount = 0;

// Weather Client
OpenWeatherMapClient weatherClient(WeatherApiKey, CityIDs, 1, IS_METRIC, WeatherLanguage);

//declairing prototypes
void configModeCallback (WiFiManager *myWiFiManager);
int8_t getWifiQuality();

ESP8266WebServer server(WEBSERVER_PORT);
ESP8266HTTPUpdateServer serverUpdater;

String WEB_ACTIONS =  "<a class='w3-bar-item w3-button' href='/'><i class='fa fa-home'></i> Home</a>"
                      "<a class='w3-bar-item w3-button' href='/configure'><i class='fa fa-cog'></i> Configure</a>"
                      "<a class='w3-bar-item w3-button' href='/configureweather'><i class='fa fa-cloud'></i> Weather</a>"
                      "<a class='w3-bar-item w3-button' href='/systemreset' onclick='return confirm(\"Do you want to reset to default settings?\")'><i class='fa fa-undo'></i> Reset Settings</a>"
                      "<a class='w3-bar-item w3-button' href='/forgetwifi' onclick='return confirm(\"Do you want to forget to WiFi connection?\")'><i class='fa fa-wifi'></i> Forget WiFi</a>"
                      "<a class='w3-bar-item w3-button' href='/update'><i class='fa fa-wrench'></i> Firmware Update</a>"
                      "<a class='w3-bar-item w3-button' href='https://github.com/Qrome' target='_blank'><i class='fa fa-question-circle'></i> About</a>";
                            
String CHANGE_FORM =  "<form class='w3-container' action='/updateconfig' method='get'><h2>Station Config:</h2>"
                      "<p><label>OctoPrint API Key (get from your server)</label><input class='w3-input w3-border w3-margin-bottom' type='text' name='octoPrintApiKey' value='%OCTOKEY%' maxlength='60'></p>"
                      "<p><label>OctoPrint Host Name (usually octopi)</label><input class='w3-input w3-border w3-margin-bottom' type='text' name='octoPrintHostName' value='%OCTOHOST%' maxlength='60'></p>"
                      "<p><label>OctoPrint Address (do not include http://)</label><input class='w3-input w3-border w3-margin-bottom' type='text' name='octoPrintAddress' value='%OCTOADDRESS%' maxlength='60'></p>"
                      "<p><label>OctoPrint Port</label><input class='w3-input w3-border w3-margin-bottom' type='text' name='octoPrintPort' value='%OCTOPORT%' maxlength='5'  onkeypress='return isNumberKey(event)'></p>"
                      "<p><label>OctoPrint User (only needed if you have haproxy or basic auth turned on)</label><input class='w3-input w3-border w3-margin-bottom' type='text' name='octoUser' value='%OCTOUSER%' maxlength='30'></p>"
                      "<p><label>OctoPrint Password </label><input class='w3-input w3-border w3-margin-bottom' type='password' name='octoPass' value='%OCTOPASS%'></p><hr>"
                      "<p><input name='isClockEnabled' class='w3-check w3-margin-top' type='checkbox' %IS_CLOCK_CHECKED%> Display Clock when printer is off</p>"
                      "<p><input name='is24hour' class='w3-check w3-margin-top' type='checkbox' %IS_24HOUR_CHECKED%> Use 24 Hour Clock (military time)</p>"
                      "<p><input name='invDisp' class='w3-check w3-margin-top' type='checkbox' %IS_INVDISP_CHECKED%> Flip display orientation</p>"
                      "<p><input name='hasPSU' class='w3-check w3-margin-top' type='checkbox' %HAS_PSU_CHECKED%> Use OctoPrint PSU control plugin for clock/blank</p>"
                      "<p>Clock Sync / Weather Refresh (minutes) <select class='w3-option w3-padding' name='refresh'>%OPTIONS%</select></p>";
                      
String THEME_FORM =   "<p>Theme Color <select class='w3-option w3-padding' name='theme'>%THEME_OPTIONS%</select></p>"
                      "<p><label>UTC Time Offset</label><input class='w3-input w3-border w3-margin-bottom' type='text' name='utcoffset' value='%UTCOFFSET%' maxlength='12'></p><hr>"
                      "<p><input name='isBasicAuth' class='w3-check w3-margin-top' type='checkbox' %IS_BASICAUTH_CHECKED%> Use Security Credentials for Configuration Changes</p>"
                      "<p><label>User ID (for this interface)</label><input class='w3-input w3-border w3-margin-bottom' type='text' name='userid' value='%USERID%' maxlength='20'></p>"
                      "<p><label>Password </label><input class='w3-input w3-border w3-margin-bottom' type='password' name='stationpassword' value='%STATIONPASSWORD%'></p>"
                      "<button class='w3-button w3-block w3-grey w3-section w3-padding' type='submit'>Save</button></form>";

String WEATHER_FORM = "<form class='w3-container' action='/updateweatherconfig' method='get'><h2>Weather Config:</h2>"
                      "<p><input name='isWeatherEnabled' class='w3-check w3-margin-top' type='checkbox' %IS_WEATHER_CHECKED%> Display Weather when printer is off</p>"
                      "<label>OpenWeatherMap API Key (get from <a href='https://openweathermap.org/' target='_BLANK'>here</a>)</label>"
                      "<input class='w3-input w3-border w3-margin-bottom' type='text' name='openWeatherMapApiKey' value='%WEATHERKEY%' maxlength='60'>"
                      "<p><label>%CITYNAME1% (<a href='http://openweathermap.org/find' target='_BLANK'><i class='fa fa-search'></i> Search for City ID</a>) "
                      "or full <a href='http://openweathermap.org/help/city_list.txt' target='_BLANK'>city list</a></label>"
                      "<input class='w3-input w3-border w3-margin-bottom' type='text' name='city1' value='%CITY1%' onkeypress='return isNumberKey(event)'></p>"
                      "<p><input name='metric' class='w3-check w3-margin-top' type='checkbox' %METRIC%> Use Metric (Celsius)</p>"
                      "<p>Weather Language <select class='w3-option w3-padding' name='language'>%LANGUAGEOPTIONS%</select></p>"
                      "<button class='w3-button w3-block w3-grey w3-section w3-padding' type='submit'>Save</button></form>"
                      "<script>function isNumberKey(e){var h=e.which?e.which:event.keyCode;return!(h>31&&(h<48||h>57))}</script>";

String LANG_OPTIONS = "<option>ar</option>"
                      "<option>bg</option>"
                      "<option>ca</option>"
                      "<option>cz</option>"
                      "<option>de</option>"
                      "<option>el</option>"
                      "<option>en</option>"
                      "<option>fa</option>"
                      "<option>fi</option>"
                      "<option>fr</option>"
                      "<option>gl</option>"
                      "<option>hr</option>"
                      "<option>hu</option>"
                      "<option>it</option>"
                      "<option>ja</option>"
                      "<option>kr</option>"
                      "<option>la</option>"
                      "<option>lt</option>"
                      "<option>mk</option>"
                      "<option>nl</option>"
                      "<option>pl</option>"
                      "<option>pt</option>"
                      "<option>ro</option>"
                      "<option>ru</option>"
                      "<option>se</option>"
                      "<option>sk</option>"
                      "<option>sl</option>"
                      "<option>es</option>"
                      "<option>tr</option>"
                      "<option>ua</option>"
                      "<option>vi</option>"
                      "<option>zh_cn</option>"
                      "<option>zh_tw</option>";

String COLOR_THEMES = "<option>red</option>"
                      "<option>pink</option>"
                      "<option>purple</option>"
                      "<option>deep-purple</option>"
                      "<option>indigo</option>"
                      "<option>blue</option>"
                      "<option>light-blue</option>"
                      "<option>cyan</option>"
                      "<option>teal</option>"
                      "<option>green</option>"
                      "<option>light-green</option>"
                      "<option>lime</option>"
                      "<option>khaki</option>"
                      "<option>yellow</option>"
                      "<option>amber</option>"
                      "<option>orange</option>"
                      "<option>deep-orange</option>"
                      "<option>blue-grey</option>"
                      "<option>brown</option>"
                      "<option>grey</option>"
                      "<option>dark-grey</option>"
                      "<option>black</option>"
                      "<option>w3schools</option>";
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
void loop() {
  
   //Get Time Update
  if((getMinutesFromLastRefresh() >= minutesBetweenDataRefresh) || lastEpoch == 0) {
    getUpdateTime();
  }

  if (lastMinute != timeClient.getMinutes() && !printerClient.isPrinting()) {
    // Check status every 60 seconds
    digitalWrite(externalLight, LOW);
    lastMinute = timeClient.getMinutes(); // reset the check value
    printerClient.getPrinterJobResults();
    printerClient.getPrinterPsuState();
    digitalWrite(externalLight, HIGH);
  } else if (printerClient.isPrinting()) {
    if (lastSecond != timeClient.getSeconds() && timeClient.getSeconds().endsWith("0")) {
      lastSecond = timeClient.getSeconds();
      // every 10 seconds while printing get an update
      digitalWrite(externalLight, LOW);
      printerClient.getPrinterJobResults();
      printerClient.getPrinterPsuState();
      digitalWrite(externalLight, HIGH);
    }
  }

  checkDisplay(); // Check to see if the printer is on or offline and change display.

  ui.update();

  if (WEBSERVER_ENABLED) {
    server.handleClient();
  }
  if (ENABLE_OTA) {
    ArduinoOTA.handle();
  }
}

void getUpdateTime() {
  digitalWrite(externalLight, LOW); // turn on the LED
  Serial.println();

  if (displayOn && DISPLAYWEATHER) {
    Serial.println("Getting Weather Data...");
    weatherClient.updateWeather();
  }

  Serial.println("Updating Time...");
  //Update the Time
  timeClient.updateTime();
  lastEpoch = timeClient.getCurrentEpoch();
  Serial.println("Local time: " + timeClient.getAmPmFormattedTime());

  digitalWrite(externalLight, HIGH);  // turn off the LED
}

boolean authentication() {
  if (IS_BASIC_AUTH && (strlen(www_username) >= 1 && strlen(www_password) >= 1)) {
    return server.authenticate(www_username, www_password);
  } 
  return true; // Authentication not required
}

void handleSystemReset() {
  if (!authentication()) {
    return server.requestAuthentication();
  }
  Serial.println("Reset System Configuration");
  if (SPIFFS.remove(CONFIG)) {
    redirectHome();
    ESP.restart();
  }
}

void handleUpdateWeather() {
  if (!authentication()) {
    return server.requestAuthentication();
  }
  DISPLAYWEATHER = server.hasArg("isWeatherEnabled");
  WeatherApiKey = server.arg("openWeatherMapApiKey");
  CityIDs[0] = server.arg("city1").toInt();
  IS_METRIC = server.hasArg("metric");
  WeatherLanguage = server.arg("language");
  writeSettings();
  isClockOn = false; // this will force a check for the display
  checkDisplay();
  lastEpoch = 0;
  redirectHome();
}

void handleUpdateConfig() {
  boolean flipOld = INVERT_DISPLAY;
  if (!authentication()) {
    return server.requestAuthentication();
  }
  OctoPrintApiKey = server.arg("octoPrintApiKey");
  OctoPrintHostName = server.arg("octoPrintHostName");
  OctoPrintServer = server.arg("octoPrintAddress");
  OctoPrintPort = server.arg("octoPrintPort").toInt();
  OctoAuthUser = server.arg("octoUser");
  OctoAuthPass = server.arg("octoPass");
  DISPLAYCLOCK = server.hasArg("isClockEnabled");
  IS_24HOUR = server.hasArg("is24hour");
  INVERT_DISPLAY = server.hasArg("invDisp");
  HAS_PSU = server.hasArg("hasPSU");
  minutesBetweenDataRefresh = server.arg("refresh").toInt();
  themeColor = server.arg("theme");
  UtcOffset = server.arg("utcoffset").toFloat();
  String temp = server.arg("userid");
  temp.toCharArray(www_username, sizeof(temp));
  temp = server.arg("stationpassword");
  temp.toCharArray(www_password, sizeof(temp));
  writeSettings();
  findMDNS();
  printerClient.getPrinterJobResults();
  printerClient.getPrinterPsuState();
  if (INVERT_DISPLAY != flipOld) {
    ui.init();
    if(INVERT_DISPLAY)     
      display.flipScreenVertically();
    ui.update();
  }
  checkDisplay();
  lastEpoch = 0;
  redirectHome();
}

void handleWifiReset() {
  if (!authentication()) {
    return server.requestAuthentication();
  }
  //WiFiManager
  //Local intialization. Once its business is done, there is no need to keep it around
  redirectHome();
  WiFiManager wifiManager;
  wifiManager.resetSettings();
  ESP.restart();
}

void handleWeatherConfigure() {
  if (!authentication()) {
    return server.requestAuthentication();
  }
  digitalWrite(externalLight, LOW);
  String html = "";

  server.sendHeader("Cache-Control", "no-cache, no-store");
  server.sendHeader("Pragma", "no-cache");
  server.sendHeader("Expires", "-1");
  server.setContentLength(CONTENT_LENGTH_UNKNOWN);
  server.send(200, "text/html", "");

  html = getHeader();
  server.sendContent(html);
  
  String form = WEATHER_FORM;
  String isWeatherChecked = "";
  if (DISPLAYWEATHER) {
    isWeatherChecked = "checked='checked'";
  }
  form.replace("%IS_WEATHER_CHECKED%", isWeatherChecked);
  form.replace("%WEATHERKEY%", WeatherApiKey);
  form.replace("%CITYNAME1%", weatherClient.getCity(0));
  form.replace("%CITY1%", String(CityIDs[0]));
  String checked = "";
  if (IS_METRIC) {
    checked = "checked='checked'";
  }
  form.replace("%METRIC%", checked);
  String options = LANG_OPTIONS;
  options.replace(">"+String(WeatherLanguage)+"<", " selected>"+String(WeatherLanguage)+"<");
  form.replace("%LANGUAGEOPTIONS%", options);
  server.sendContent(form);
  
  html = getFooter();
  server.sendContent(html);
  server.sendContent("");
  server.client().stop();
  digitalWrite(externalLight, HIGH);
}

void handleConfigure() {
  if (!authentication()) {
    return server.requestAuthentication();
  }
  digitalWrite(externalLight, LOW);
  String html = "";

  server.sendHeader("Cache-Control", "no-cache, no-store");
  server.sendHeader("Pragma", "no-cache");
  server.sendHeader("Expires", "-1");
  server.setContentLength(CONTENT_LENGTH_UNKNOWN);
  server.send(200, "text/html", "");

  html = getHeader();
  server.sendContent(html);
  
  String form = CHANGE_FORM;
  
  form.replace("%OCTOKEY%", OctoPrintApiKey);
  form.replace("%OCTOHOST%", OctoPrintHostName);
  form.replace("%OCTOADDRESS%", OctoPrintServer);
  form.replace("%OCTOPORT%", String(OctoPrintPort));
  form.replace("%OCTOUSER%", OctoAuthUser);
  form.replace("%OCTOPASS%", OctoAuthPass);
  String isClockChecked = "";
  if (DISPLAYCLOCK) {
    isClockChecked = "checked='checked'";
  }
  form.replace("%IS_CLOCK_CHECKED%", isClockChecked);
  String is24hourChecked = "";
  if (IS_24HOUR) {
    is24hourChecked = "checked='checked'";
  }
  form.replace("%IS_24HOUR_CHECKED%", is24hourChecked);
  String isInvDisp = "";
  if (INVERT_DISPLAY) {
    isInvDisp = "checked='checked'";
  }
  form.replace("%IS_INVDISP_CHECKED%", isInvDisp);
  String hasPSUchecked = "";
  if (HAS_PSU) {
    hasPSUchecked = "checked='checked'";
  }
  form.replace("%HAS_PSU_CHECKED%", hasPSUchecked);
  
  String options = "<option>10</option><option>15</option><option>20</option><option>30</option><option>60</option>";
  options.replace(">"+String(minutesBetweenDataRefresh)+"<", " selected>"+String(minutesBetweenDataRefresh)+"<");
  form.replace("%OPTIONS%", options);

  server.sendContent(form);

  form = THEME_FORM;
  
  String themeOptions = COLOR_THEMES;
  themeOptions.replace(">"+String(themeColor)+"<", " selected>"+String(themeColor)+"<");
  form.replace("%THEME_OPTIONS%", themeOptions);
  form.replace("%UTCOFFSET%", String(UtcOffset));
  String isUseSecurityChecked = "";
  if (IS_BASIC_AUTH) {
    isUseSecurityChecked = "checked='checked'";
  }
  form.replace("%IS_BASICAUTH_CHECKED%", isUseSecurityChecked);
  form.replace("%USERID%", String(www_username));
  form.replace("%STATIONPASSWORD%", String(www_password));

  server.sendContent(form);
  
  html = getFooter();
  server.sendContent(html);
  server.sendContent("");
  server.client().stop();
  digitalWrite(externalLight, HIGH);
}

void displayMessage(String message) {
  digitalWrite(externalLight, LOW);

  server.sendHeader("Cache-Control", "no-cache, no-store");
  server.sendHeader("Pragma", "no-cache");
  server.sendHeader("Expires", "-1");
  server.setContentLength(CONTENT_LENGTH_UNKNOWN);
  server.send(200, "text/html", "");
  String html = getHeader();
  server.sendContent(String(html));
  server.sendContent(String(message));
  html = getFooter();
  server.sendContent(String(html));
  server.sendContent("");
  server.client().stop();
  
  digitalWrite(externalLight, HIGH);
}

void redirectHome() {
  // Send them back to the Root Directory
  server.sendHeader("Location", String("/"), true);
  server.sendHeader("Cache-Control", "no-cache, no-store");
  server.sendHeader("Pragma", "no-cache");
  server.sendHeader("Expires", "-1");
  server.send(302, "text/plain", "");
  server.client().stop();
}

String getHeader() {
  return getHeader(false);
}
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

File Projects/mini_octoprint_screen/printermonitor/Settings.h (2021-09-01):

/** The MIT License (MIT)

Copyright (c) 2018 David Payne

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
THE SOFTWARE IS PROVIDED "AS IS", WITHOUT WARRANTY OF ANY KIND, EXPRESS OR
IMPLIED, INCLUDING BUT NOT LIMITED TO THE WARRANTIES OF MERCHANTABILITY,
FITNESS FOR A PARTICULAR PURPOSE AND NONINFRINGEMENT. IN NO EVENT SHALL THE
AUTHORS OR COPYRIGHT HOLDERS BE LIABLE FOR ANY CLAIM, DAMAGES OR OTHER
LIABILITY, WHETHER IN AN ACTION OF CONTRACT, TORT OR OTHERWISE, ARISING FROM,
OUT OF OR IN CONNECTION WITH THE SOFTWARE OR THE USE OR OTHER DEALINGS IN THE
SOFTWARE.
*/

// Additional Contributions:
/* 15 Jan 2019 : Owen Carter : Add psucontrol setting */

/******************************************************************************
 * Printer Monitor is designed for the Wemos D1 ESP8266
 * Wemos D1 Mini:  https://amzn.to/2qLyKJd
 * 0.96" OLED I2C 128x64 Display (12864) SSD1306
 * OLED Display:  https://amzn.to/2JDEAUF
 ******************************************************************************/
/******************************************************************************
 * NOTE: The settings here are the default settings for the first loading.  
 * After loading you will manage changes to the settings via the Web Interface.  
 * If you want to change settings again in the settings.h, you will need to 
 * erase the file system on the Wemos or use the “Reset Settings” option in 
 * the Web Interface.
 ******************************************************************************/

#include <ESP8266WiFi.h>
#include <ESP8266WebServer.h>
#include <WiFiManager.h>
#include <ESP8266mDNS.h>
#include <ArduinoOTA.h>
#include <ESP8266HTTPUpdateServer.h>
#include "TimeClient.h"
#include "OctoPrintClient.h"
#include "OpenWeatherMapClient.h"
#include "WeatherStationFonts.h"
#include "FS.h"
#include "SH1106Wire.h"
#include "SSD1306Wire.h"
#include "OLEDDisplayUi.h"

//******************************
// Start Settings
//******************************

// OctoPrint Monitoring -- Monitor your 3D printer OctoPrint Server
String OctoPrintApiKey = "0C8140FDB1B7482CB92361FC48473FBF";   // ApiKey from your User Account on OctoPrint
String OctoPrintHostName = "octopi";// Default 'octopi' -- or hostname if different (optional if your IP changes)
String OctoPrintServer = "";   // IP or Address of your OctoPrint Server (DO NOT include http://)
int OctoPrintPort = 80;        // the port you are running your OctoPrint server on (usually 80);
String OctoAuthUser = "";      // only used if you have haproxy or basic athentintication turned on (not default)
String OctoAuthPass = "";      // only used with haproxy or basic auth (only needed if you must authenticate)

// Weather Configuration
boolean DISPLAYWEATHER = true; // true = show weather when not printing / false = no weather
String WeatherApiKey = "271efb0cbf1b16ae131a15aa6b26ded3"; // Your API Key from http://openweathermap.org/
// Default City Location (use http://openweathermap.org/find to find city ID)
int CityIDs[] = { 3175677 }; //Only USE ONE for weather marquee
boolean IS_METRIC = false; // false = Imperial and true = Metric
// Languages: ar, bg, ca, cz, de, el, en, fa, fi, fr, gl, hr, hu, it, ja, kr, la, lt, mk, nl, pl, pt, ro, ru, se, sk, sl, es, tr, ua, vi, zh_cn, zh_tw
String WeatherLanguage = "it";  //Default (en) English

// Webserver
const int WEBSERVER_PORT = 80; // The port you can access this device on over HTTP
const boolean WEBSERVER_ENABLED = true;  // Device will provide a web interface via http://[ip]:[port]/
boolean IS_BASIC_AUTH = true;  // true = require athentication to change configuration settings / false = no auth
char* www_username = "admin";  // User account for the Web Interface
char* www_password = "password";  // Password for the Web Interface

// Date and Time
float UtcOffset = -7; // Hour offset from GMT for your timezone
boolean IS_24HOUR = false;     // 23:00 millitary 24 hour clock
int minutesBetweenDataRefresh = 15;
boolean DISPLAYCLOCK = true;   // true = Show Clock when not printing / false = turn off display when not printing

// Display Settings
const int I2C_DISPLAY_ADDRESS = 0x3c; // I2C Address of your Display (usually 0x3c or 0x3d)
const int SDA_PIN = D2;
const int SCL_PIN = D5;
boolean INVERT_DISPLAY = false; // true = pins at top | false = pins at the bottom
//#define DISPLAY_SH1106       // Uncomment this line to use the SH1106 display -- SSD1306 is used by default and is most common

// LED Settings
const int externalLight = LED_BUILTIN; // Set to unused pin, like D1, to disable use of built-in LED (LED_BUILTIN)

// PSU Control
boolean HAS_PSU = false; // Set to true if https://github.com/kantlivelong/OctoPrint-PSUControl/ in use

// OTA Updates
boolean ENABLE_OTA = true;     // this will allow you to load firmware to the device over WiFi (see OTA for ESP8266)
String OTA_Password = "";      // Set an OTA password here -- leave blank if you don't want to be prompted for password

//******************************
// End Settings
//******************************
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

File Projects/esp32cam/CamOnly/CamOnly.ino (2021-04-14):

// CAM Only Portions Copyright 2019 Robert Mech - rwmech@gmail.com 
// Based on the WebServer reference application by Espressif Systems.
// This module has been modified to strip down to a simple stream or capture and 
// added a watchdog timer to the stream.  If the stream is shut down for any reason
// hangs the watchdog reboots the ESP.  This compensates for some ESP32-CAM's that 
// lock up occasionally.  

#include "esp_camera.h"
#include <WiFi.h>
#include "esp_system.h"
#include <ESPmDNS.h>

//
// WARNING!!! Make sure that you have either selected ESP32 Wrover Module,
//            or another board which has PSRAM enabled
//

// Select camera model
//#define CAMERA_MODEL_WROVER_KIT
//#define CAMERA_MODEL_ESP_EYE
//#define CAMERA_MODEL_M5STACK_PSRAM
//#define CAMERA_MODEL_M5STACK_WIDE
#define CAMERA_MODEL_AI_THINKER

#include "camera_pins.h"

// Configuration - Modify the device name and network SSID and password. 
const char* DEVICE_NAME = "ESP32_CAM01";
const char* ssid = "Casa_Fabio";
const char* password = "Fabio1964";
// End Configuration

const int lampledPin = 4;

void startCameraServer();

void setup() {
  Serial.begin(115200);
  Serial.setDebugOutput(true);
  Serial.println();
  
  pinMode(lampledPin, OUTPUT);
  
  camera_config_t config;
  config.ledc_channel = LEDC_CHANNEL_0;
  config.ledc_timer = LEDC_TIMER_0;
  config.pin_d0 = Y2_GPIO_NUM;
  config.pin_d1 = Y3_GPIO_NUM;
  config.pin_d2 = Y4_GPIO_NUM;
  config.pin_d3 = Y5_GPIO_NUM;
  config.pin_d4 = Y6_GPIO_NUM;
  config.pin_d5 = Y7_GPIO_NUM;
  config.pin_d6 = Y8_GPIO_NUM;
  config.pin_d7 = Y9_GPIO_NUM;
  config.pin_xclk = XCLK_GPIO_NUM;
  config.pin_pclk = PCLK_GPIO_NUM;
  config.pin_vsync = VSYNC_GPIO_NUM;
  config.pin_href = HREF_GPIO_NUM;
  config.pin_sscb_sda = SIOD_GPIO_NUM;
  config.pin_sscb_scl = SIOC_GPIO_NUM;
  config.pin_pwdn = PWDN_GPIO_NUM;
  config.pin_reset = RESET_GPIO_NUM;
  config.xclk_freq_hz = 20000000;
  config.pixel_format = PIXFORMAT_JPEG;
  //init with high specs to pre-allocate larger buffers
  if(psramFound()){
    Serial.println("PSRAM Found()");
    config.frame_size = FRAMESIZE_VGA;
    config.jpeg_quality = 10;
    config.fb_count = 4;
  } else {
    config.frame_size = FRAMESIZE_VGA;
    config.jpeg_quality = 10;
    config.fb_count = 2;
  }

#if defined(CAMERA_MODEL_ESP_EYE)
  pinMode(13, INPUT_PULLUP);
  pinMode(14, INPUT_PULLUP);
#endif

  // camera init
  esp_err_t err = esp_camera_init(&config);
  if (err != ESP_OK) {
    Serial.printf("Camera init failed with error 0x%x", err);
    Serial.printf("\n\nRebooting in 3 seconds...\n");
    delay(3000);
    esp_restart();

    return;
  }

  sensor_t * s = esp_camera_sensor_get();
  //initial sensors are flipped vertically and colors are a bit saturated
  if (s->id.PID == OV3660_PID) {
    s->set_vflip(s, 1);//flip it back
    s->set_brightness(s, 1);  //up the blightness just a bit
    s->set_saturation(s, -2); //lower the saturation
    s->set_sharpness(s, 2);   //Up THe sharpness
  }
  //drop down frame size for higher initial frame rate
  s->set_framesize(s, FRAMESIZE_VGA);

#if defined(CAMERA_MODEL_M5STACK_WIDE)
  s->set_vflip(s, 1);
  s->set_hmirror(s, 1);
#endif

  WiFi.begin(ssid, password);

  while (WiFi.status() != WL_CONNECTED) {
    delay(500);
    Serial.print(".");
  }
  Serial.println("");
  Serial.println("WiFi connected");
  startCameraServer();

  Serial.print("Camera Ready! Use 'http://");
  Serial.print(WiFi.localIP());
  Serial.println("' to connect");
  WiFi.setHostname(DEVICE_NAME);
  digitalWrite(lampledPin, LOW);
}

void AdvertiseServices(const char *MyName)
{
  if (MDNS.begin(MyName))
  {
    Serial.println(F("mDNS responder started"));
    Serial.print(F("I am: "));
    Serial.println(MyName);
 
    // Add service to MDNS-SD
    MDNS.addService("http", "tcp", 80);
  }
  else
  {
    while (1) 
    {
      Serial.println(F("Error setting up MDNS responder"));
      delay(1000);
    }
  }
}

void loop() {
  AdvertiseServices(DEVICE_NAME);
  delay(2000); //simulate work
}

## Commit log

2021-03-26 Added chain for GH5 box
    [maglia finale v1.stl, maglia_chain_10x25_v2.stl]
2021-03-26 Added useful links
    [3D Print Price Calculator.xlsx]
2021-03-26 Chain and case structure
    [angolo n 2 con buchi porta ghost v1da 4 mm.stl, angolo porta ghost v1 da 4mm.stl, cerniera v1 da 4mm.stl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]
2021-03-30 Added projects & other features
    [FilamentHolder.stl, Filament_Cleaner_sibmaker.stl, FlyingBear_G5_bed.stl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]
2021-03-30 other fixes
    [FlyingBear_G5_bed.stl]
2021-03-30 Upload supporto bobina
    [Porta Bobina.stl]
2021-04-01 Added plexiglass case
    [FBG5 Cover.stl]
2021-04-08 Upload updated machine cover and new firmware (only for tmc 2209)
    [10_1.stl, 10_2.stl, 22.stl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]
2021-04-14 Added prusaslicer MKS version
    [Front Wall With Hole.dwg, Front Wall With Hole.dxf, Front Wall With Hole.stl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]
2021-04-14 Added esp32 cam
2021-04-20 Added some firmwares
    [Sunlu_Dryer_Objects.stl]
2021-04-21 Some new things
    [Esp32 gopro.stl]
2021-04-22 Added octoprint relay box
    [Octoprint box bottom.stl, Octoprint box upper.stl]
2021-04-22 TMC2209 replacement
    [Cacciavite vref.stl]
2021-04-22 Prusaslicer changes
    [FlyingBear_G5_bed.stl]
2021-04-23 Fix PSU control README
    [Octoprint_box_bottom.stl, Octoprint_box_upper.stl]
2021-04-27 Added russian upgrades from "chuchatv"
    [BLTouch holder.ipt, BLTouch holder.stl, BMG connector for factory.ipt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]
2021-04-27 chucha upgrades
    [Estimate.xlsx]
2021-04-27 Added DXF file format
    [Box roof DXF.dxf, Cap DXF.dxf, Front Panel DXF.dxf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]
2021-04-27 CHUCHATV estimate pdf version
    [Estimate.xlsx]
2021-04-28 Z axis upgrade
    [Bottom_part.stl, Upper_part.stl, Z_screw_holder.stl]
2021-04-29 Added Octoprint_box_bottom v2
    [Octoprint_box_bottom_v2.stl]
2021-05-05 Some updates
    [Base Parte A.stl, Base Parte B.stl, Base Parte C.stl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]
2021-05-05 Anti wobble 2
    [Assemblaggio dado.SLDASM, Assemblaggio dado.STEP, Bottom_part.stl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]
2021-05-12 Some stuff & firmware update
    [Filament_Cleaner_sibmaker.stl, corner_buttom_back_left.stl, corner_buttom_back_right.stl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]
2021-05-13 Upload flyingbear ghost 5 pcb head
2021-05-19 Added Flyingbear ghost 5 direct head + other things
    [Test catena mia v2.stl, Top Cover.stl, inizio catena mia.stl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]
2021-05-25 Added raspberry pi infrared camera case
    [Octoprint_box_uppe_with-camera-holes.stl, Staffa_Snodo.stl, base_cover.stl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]
2021-05-27 Added raspberry cam
    [cam_angle_high.stl, corto.stl, gancio basso.stl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]
2021-06-04 Added manual caliber in project
    [Extender_40.STL, Extender_45.STL, Extender_50.STL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]
2021-06-30 Added projects and other things
    [2GT 5mm 0.ipt, 2GT 5mm 0.stp, 2GT 5mm 2.ipt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]
2021-06-30 Added printer profiles backup
    [FBG5_PRINTER_PROFILE.3mf]
2021-09-01 Added new guide: smart led
    [Case_ralay_Bouton_v2.stl, Case_ralay_Case_v2.stl, Case_ralay_Couvercle_v2.stl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]
